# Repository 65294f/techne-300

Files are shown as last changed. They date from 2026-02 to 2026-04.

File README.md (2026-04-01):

<h1 align="center">Techne-300</h1>

<p align="center">
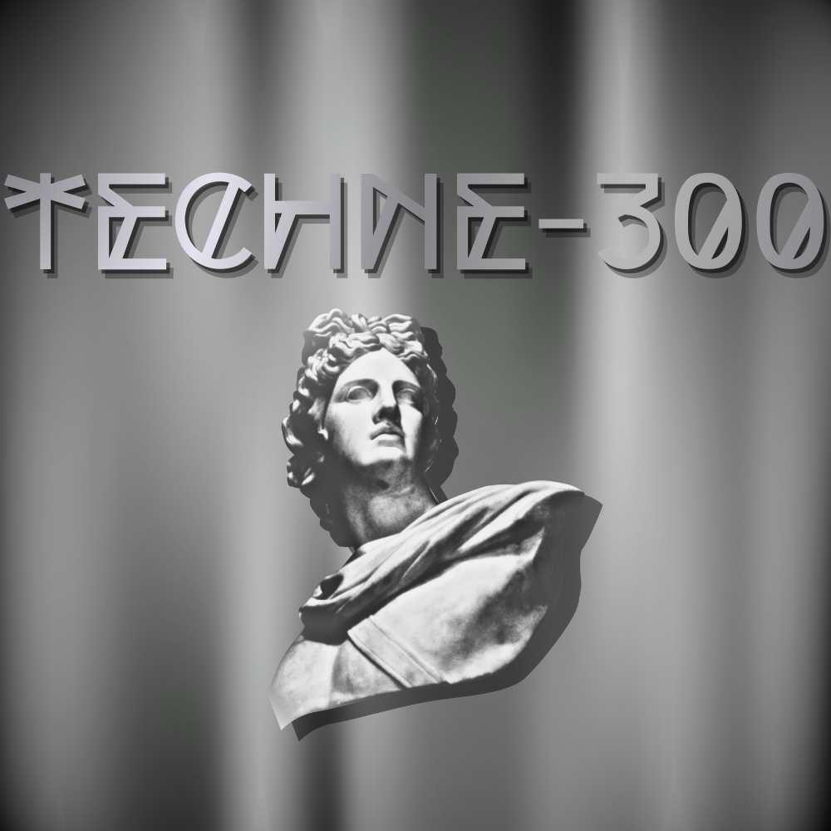
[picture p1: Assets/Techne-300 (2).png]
  
</p>

Inspired by builds like Chris Borges' printed CNC. Using thin-walled prints with threaded rods and concrete to add weight and structure on a budget. 
The Techne-300 is a simple CNC mill primarily made of 3D printed and readily available parts. It is designed for consistent milling for prototyping. 

<h4 align="center">
  BOM at the bottom of the README and 
<a href="https://docs.github.com)](https://github.com/65294f/techne-300/blob/main/Techne-300-part-list.csv">Part-list for amounts, STLs, filament, and print time for 3D printed parts.</a>
</h4>
<h3 align="center"> in the .csv BOM parts marked (purchased) are not added to the total cost and do not need funding.</h3>

I wanted to make this to help my FTC team quickly prototype parts that would normally take weeks to make or get. We have tons of innovative design ideas that are impossible for us to bring into reality without a CNC machine. This build is supposed to be iterated and improved over time for whatever application is needed. I wanted to make an interesting machine, something that hadn’t been made before — that’s why I went for the movement and the structure that I designed.

<h1 align="center">Design</h1>
This design started on paper, just small ideas that compounded into the machine you see now.

<p align="center">
  wiring
</p>

<p align="center">
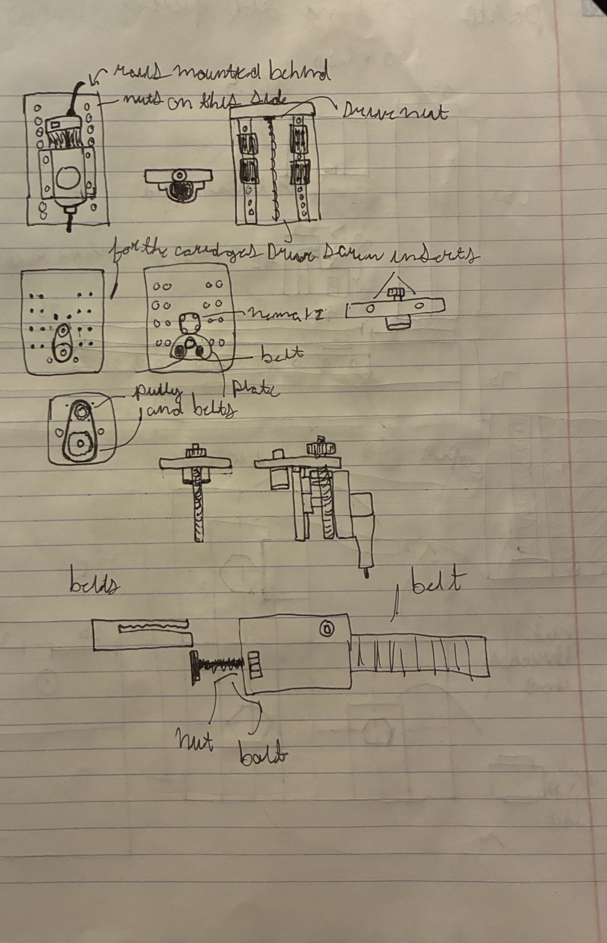
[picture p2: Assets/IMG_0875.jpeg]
  
</p>

<h1 align="center">Structure</h1>

The structure was inspired by Chris Borges' 3D printed CNC machine. It uses concrete-filled thin-walled 3D parts to add weight and structure while keeping prices low. To add more structure for the parts, 5/16 in threaded rod is run through the thin-walled parts and secured with nuts. 

<p align="center">
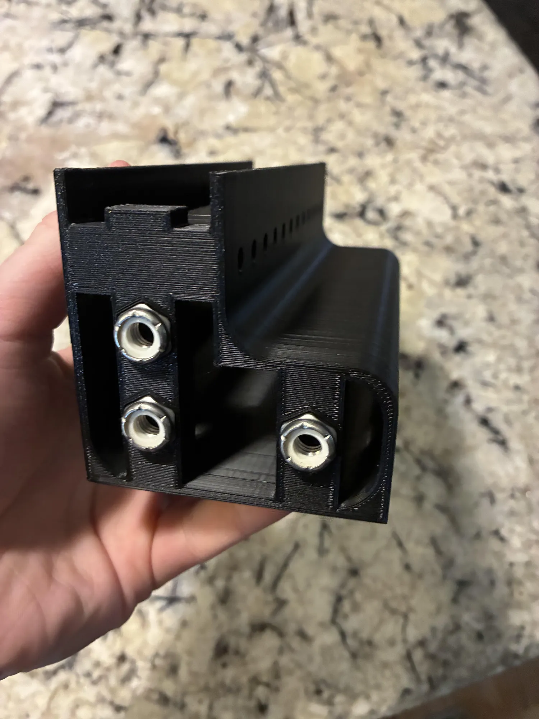
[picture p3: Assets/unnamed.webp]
  
</p>

The parts' thin walls are connected to prevent spreading from the weight of the concrete. This came after a few iterations of printed prototypes. 
The main structure is made of a single 3D printed part repeated 14 times with repeated corner pieces to reduce complexity. 

<p align="center">
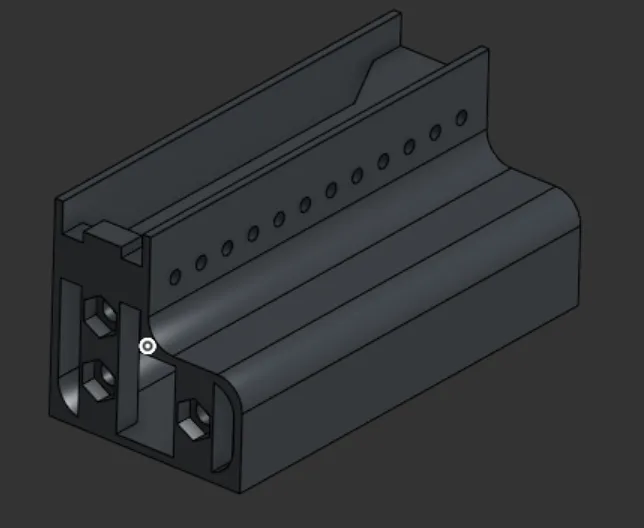
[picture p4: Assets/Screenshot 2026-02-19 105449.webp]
  
</p>

<p align="center">
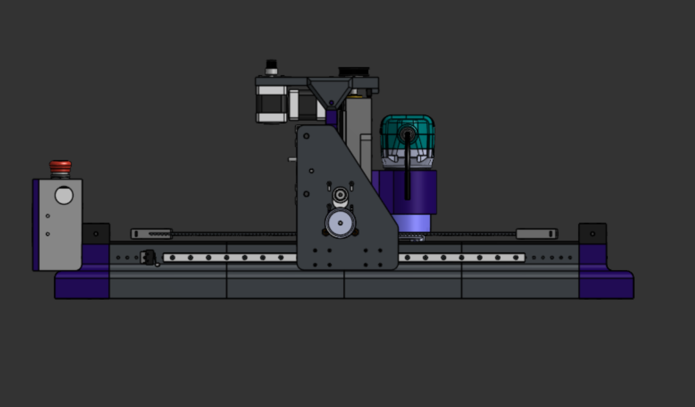
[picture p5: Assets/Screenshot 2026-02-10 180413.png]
  
</p>

<p align="center">
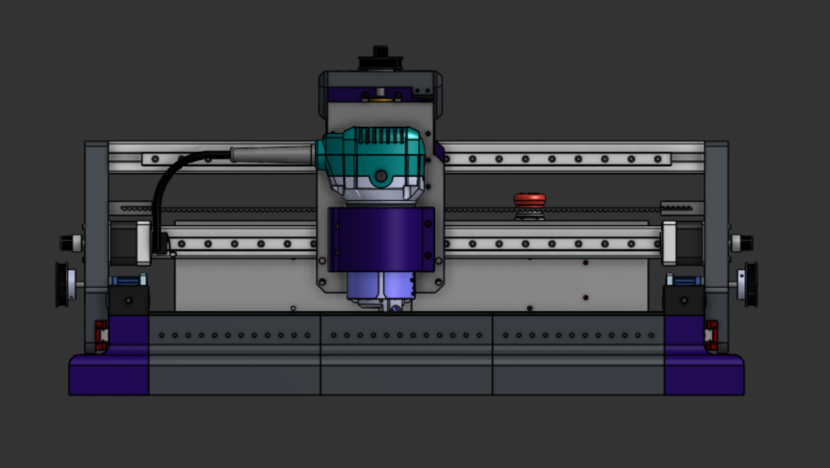
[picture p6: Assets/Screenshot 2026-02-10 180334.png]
  
</p>

<p align="center">
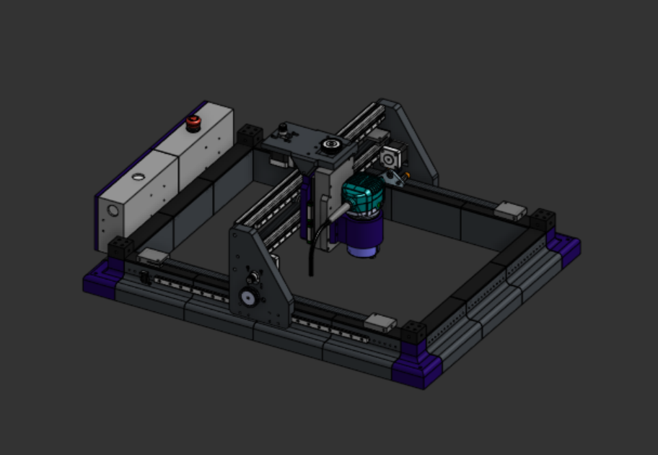
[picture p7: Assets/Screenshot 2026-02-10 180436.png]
  
</p>

<h1 align="center">Construction</h1>
The construction consists of two main parts: the base and the gantry. A full build guide will be able to be eventually found <a href="https://docs.google.com/document/d/1vw35Qro_V9RjRC6oUcMq-4XFSKVUzZ7_NZ20Waa5mPg/edit?usp=sharing"> HERE! 

<h1 align="center">Base</h3>

For the base, 3 nuts are placed in the holes and threaded rod is run through 2 groups of 3 and 2 groups of 4. The pieces are then assembled with the corners and glued/melted together. 

<p align="center">
  wiring
</p>

<p align="center">
  wiring
</p>

Concrete (concrete used cannot have any aggregate or the pour will be very difficult) is then poured into the empty space, and the back side of an electric sander is used to make sure that no air bubbles or unfilled spaces are left. The caps are pressed on and it is left to set. Heat-set inserts are pushed into the long side and then the linear rails are secured to the sides with M3 screws.

<h1 align="center">Gantry</h3>

The first step of gantry construction is screwing in the main 3D printed gantry pieces into the linear slides. The T-slot extrusion is then tapped and the linear rails are secured on with the T-nuts. You then screw the extrusion between the main gantry pieces. The Z-axis is then secured onto the linear rails.

<p align="center">
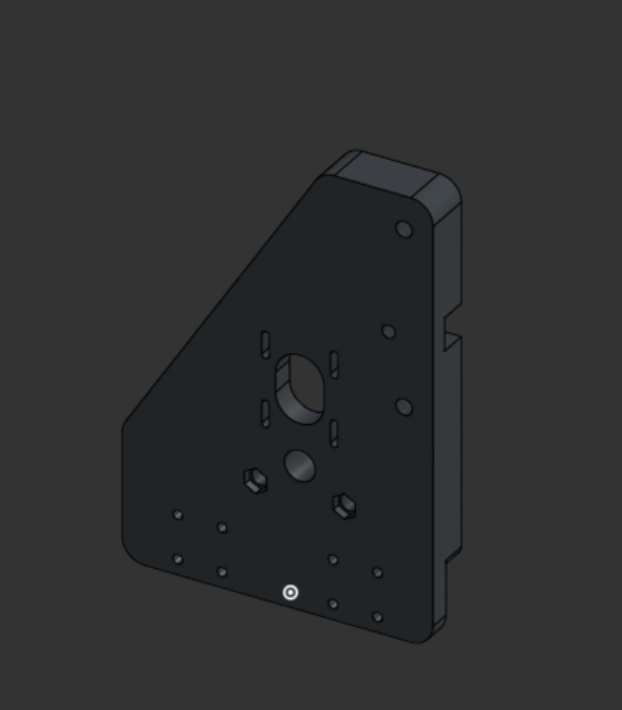
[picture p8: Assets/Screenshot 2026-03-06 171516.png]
  
</p>

<p align="center">
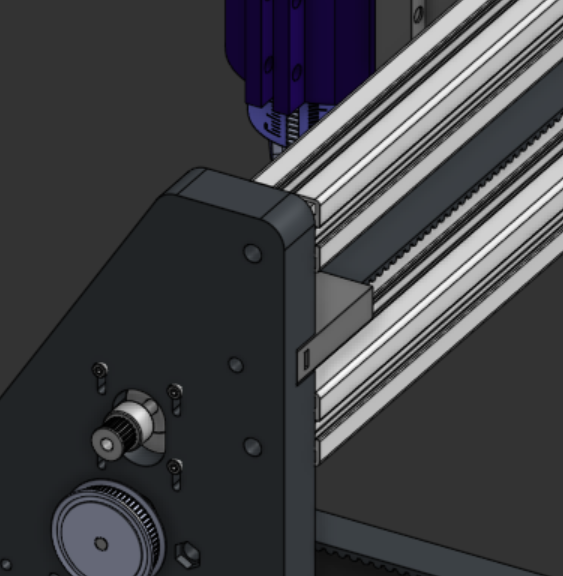
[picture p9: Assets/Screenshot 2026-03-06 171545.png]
  
</p>

For this project I used:
<h4>
<a href="https://github.com/winder/Universal-G-Code-Sender">Universal G-Code Sender</a>
</h4>
<h4>
<a href="https://www.onshape.com/en/">Onshape</a>
</h4>
For inspiration: <h4>
<a href="https://www.youtube.com/watch?v=L8t82OQXefM">Chris Borges</a>
and 
<a href="https://www.youtube.com/watch?v=ctyLjOHg7Ag">Ivan Miranda</a>
</h4>

<h1 align="center">Bill of Materials</h1>
<h3 align="center">Parts marked (purchased) are not added to the total cost and do not need funding.</h3>

| Part | Link | Amount | Price |
|---|---|---|---|
| (Purchased) Threaded Rod 5/16in. x 6 ft | [homedepot](https://www.homedepot.com/p/Everbilt-5-16-in-x-6-ft-Zinc-Plated-Steel-Coarse-Threaded-Rod-23021/332733633) | x4 | $23.92 |
| (Purchased) Hex Nut 5/16 in. | [homedepot](https://www.homedepot.com/p/Everbilt-5-16-in-18-Zinc-Plated-Hex-Nut-100-Pack-801740/204274104) | x1 | $2.18 |
| (Purchased) Concrete Mix 80 lb. | [homedepot](https://www.homedepot.com/p/Quikrete-80-lb-Concrete-Mix-110180/100318511) | x1 | $5.98 |
| MGN12 Linear Rail Guide 500mm | [aliexpress](https://www.aliexpress.us/item/3256806930596644.html) | x2 | $98.00 |
| Nema 17 Stepper | [amazon](https://www.amazon.com/NEMA17-Stepper-Torque-Bipolar-MOTOU/dp/B07RZHWYQ9) | x1 | $32.99 |
| Aluminum 5mm Bore 2GT Pulley | [aliexpress](https://www.aliexpress.us/item/2251832795479948.html) | x3 | $12.18 |
| 5mm x 330 mm steel rod | [aliexpress](https://www.aliexpress.us/item/3256805290944526.html) | x1 | $3.15 |
| 10 Teeth HTD 5M | [aliexpress](https://www.aliexpress.us/item/3256807463348700.html) | x3 | $16.11 |
| Ball Bearings | [aliexpress](https://www.aliexpress.us/item/3256805135171835.html) | x3 | $5.07 |
| Flanged Ball Bearings | [aliexpress](https://www.aliexpress.us/item/3256808460014090.html) | x1 | $5.61 |
| 150mm Lead Screw | [aliexpress](https://www.aliexpress.us/item/3256801899005803.html) | x1 | $4.99 |
| 60 Teeth Pulley | [aliexpress](https://www.aliexpress.us/item/3256808471298920.html) | x1 | $3.39 |
| Power Supply | [aliexpress](https://www.aliexpress.us/item/3256802657514911.html) | x1 | $5.01 |
| CNC Shield | [aliexpress](https://www.aliexpress.us/item/3256806291794239.html) | x1 | $8.27 |
| Emergency Stop | [aliexpress](https://www.aliexpress.us/item/3256810118000497.html) | x1 | $3.23 |
| Timing Belt | [aliexpress](https://www.aliexpress.us/item/3256810100027326.html) | x1 | $7.11 |
| 150mm Linear Rail | [amazon](https://www.amazon.com/uxcell-Sliding-Carriage-Bearing-Printers/dp/B0D54LDBHN) | x1 | $18.69 |
| 20x20 extrusion | [jlcmc](https://jlcmc.com/product/s/T01/TXCX/extruded-aluminum-t-slot-15-series(gb)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) | x1 | $1.89 |
| (Purchased) Makita router | [inventables](https://www.inventables.com/products/makita-router?variant=41037047398457) | x1 | N/A |
| Heated inserts | [amazon](https://www.amazon.com/Yaocom-Inserts-Threaded-Printing-Components/dp/B0DG59PW2R) | x1 | $9.99 |
| Micro Limit Switch | [amazon](https://us.amazon.com/HiLetgo-KW12-3-Roller-Switch-Normally/dp/B07X142VGC) | x1 | $5.99 |
| M3 T Nuts | [amazon](https://www.amazon.com/HELIFOUNER-Pieces-2020-Aluminum-Profile/dp/B0B1LTNX7F) | x1 | $4.99 |
| (Purchased) M3 Screws Assortment Kit | [amazon](https://www.amazon.com/Screws-Assortment-Plated-Socket-Washers/dp/B0D3X5CT2J) | x1 | $7.99 |
| (Purchased) 4kg PLA | [amazon](https://us.amazon.com/SUNLU-2-0-Filament-Stronger-Dimensional/dp/B0DGXFXP45) | x1 | $42.99 |

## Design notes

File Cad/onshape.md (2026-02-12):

<h1 align="center">onshape cad link</h1>

<h4 align="center">
<a href="https://cad.onshape.com/documents/1772326699bf1130a6529598/w/907cdc5ddbb09328c3f2774f/e/d35b3060a68eec815520a78b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">Onshape</a>
</h4>

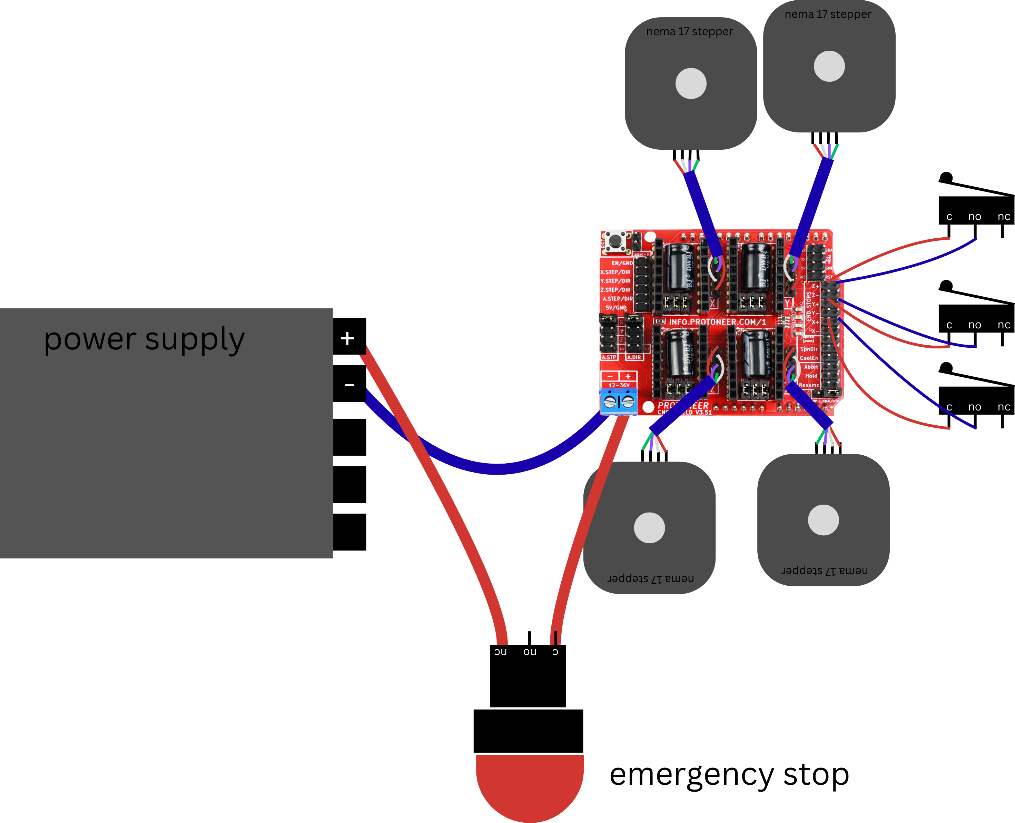
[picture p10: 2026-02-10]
c.png

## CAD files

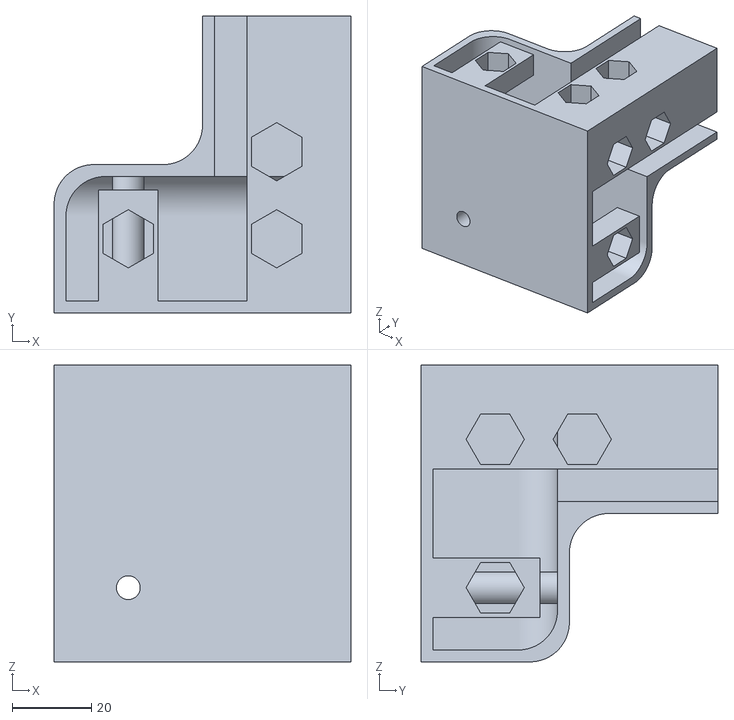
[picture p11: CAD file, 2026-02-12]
Parts/plastic print - Part 10.stl
75.0 x 75.1 x 75.0

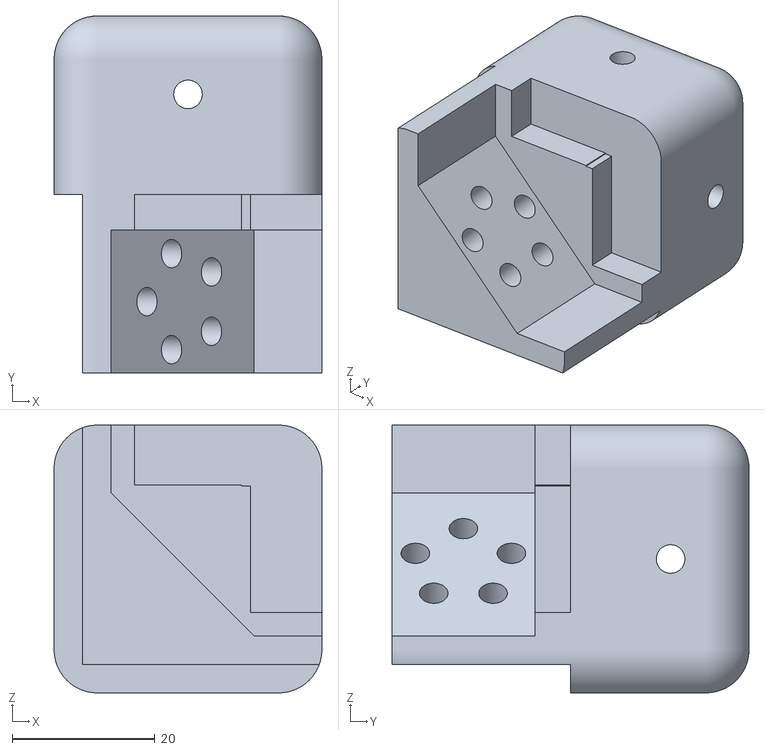
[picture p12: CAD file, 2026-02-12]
Parts/plastic print - Part 41.stl
37.5 x 50.0 x 37.5

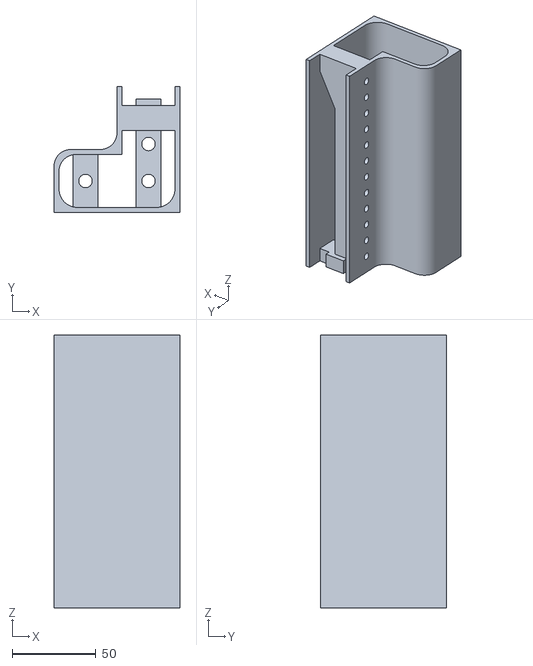
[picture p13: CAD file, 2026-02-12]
Parts/plastic print - Part 9.stl
75.0 x 75.0 x 162.5

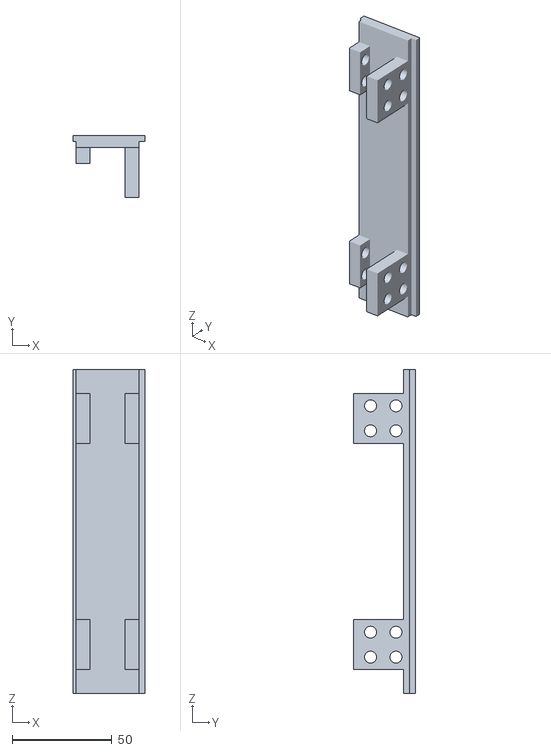
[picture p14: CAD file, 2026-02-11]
Parts/plastic print - Part 11.stl
36.0 x 31.0 x 162.5

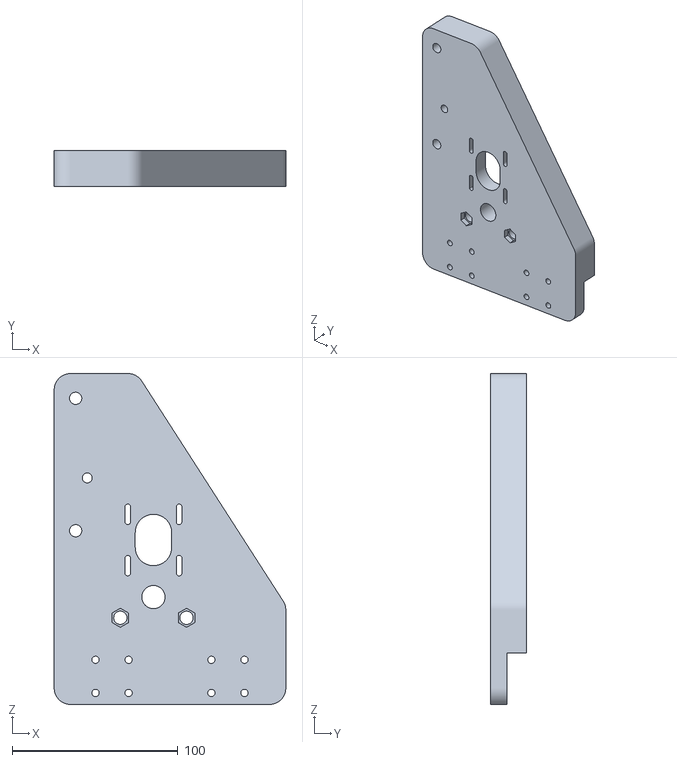
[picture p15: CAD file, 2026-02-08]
Parts/techne-300 - Part 26.stl
140.0 x 22.0 x 200.0

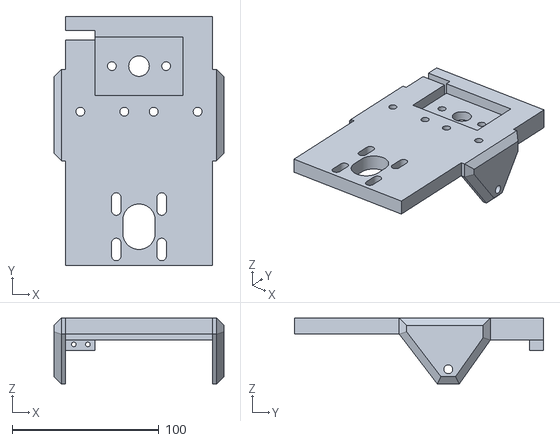
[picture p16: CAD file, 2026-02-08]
Parts/techne-300 - Part 24.stl
116.0 x 170.0 x 45.0

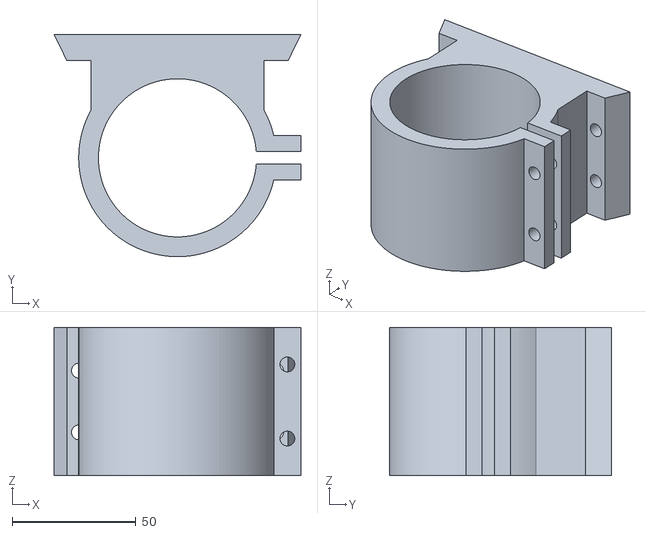
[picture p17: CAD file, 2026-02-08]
Parts/techne-300 - Part 17.stl
100.0 x 90.0 x 60.0

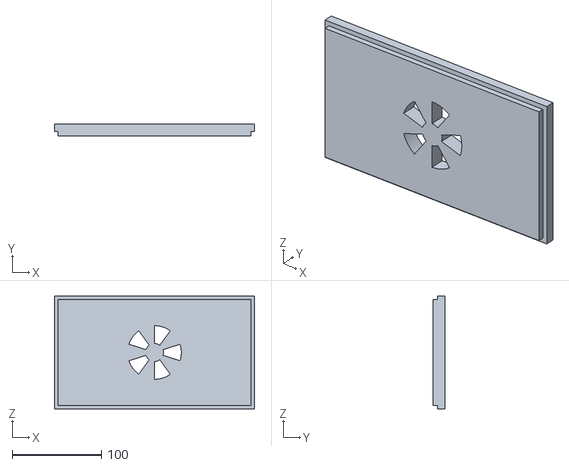
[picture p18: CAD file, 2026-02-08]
Parts/techne-300 - Part 40.stl
223.5 x 13.0 x 126.0

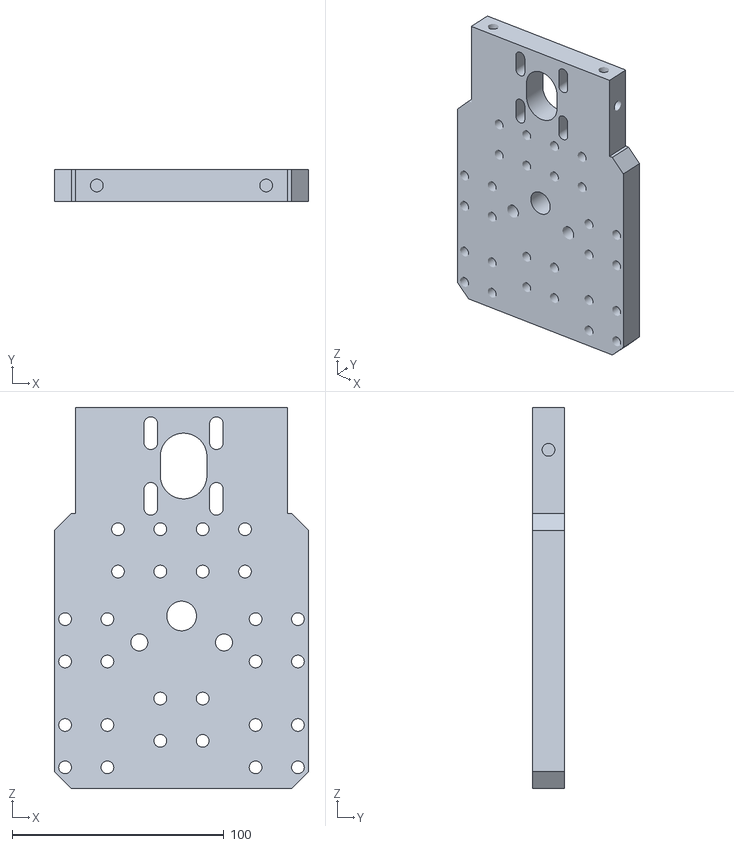
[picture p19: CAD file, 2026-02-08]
Parts/techne-300 - Part 15.stl
120.0 x 15.0 x 180.0

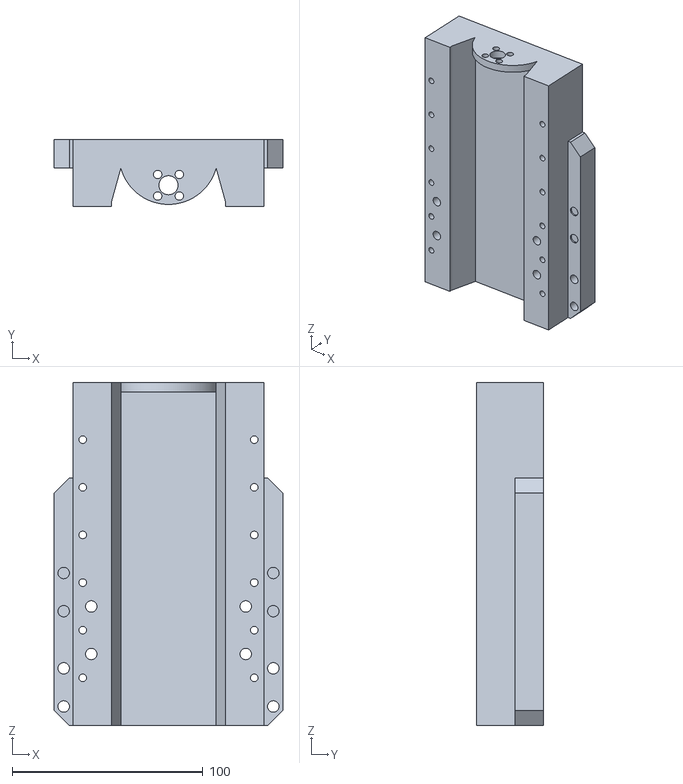
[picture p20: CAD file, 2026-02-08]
Parts/techne-300 - Part 16.stl
120.0 x 35.2 x 180.0

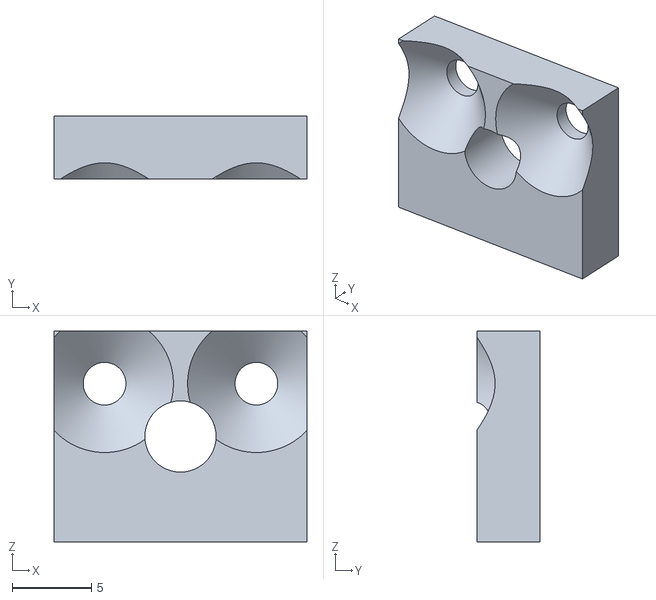
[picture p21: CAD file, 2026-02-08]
Parts/techne-300 - Part 35.stl
16.0 x 4.00 x 13.3

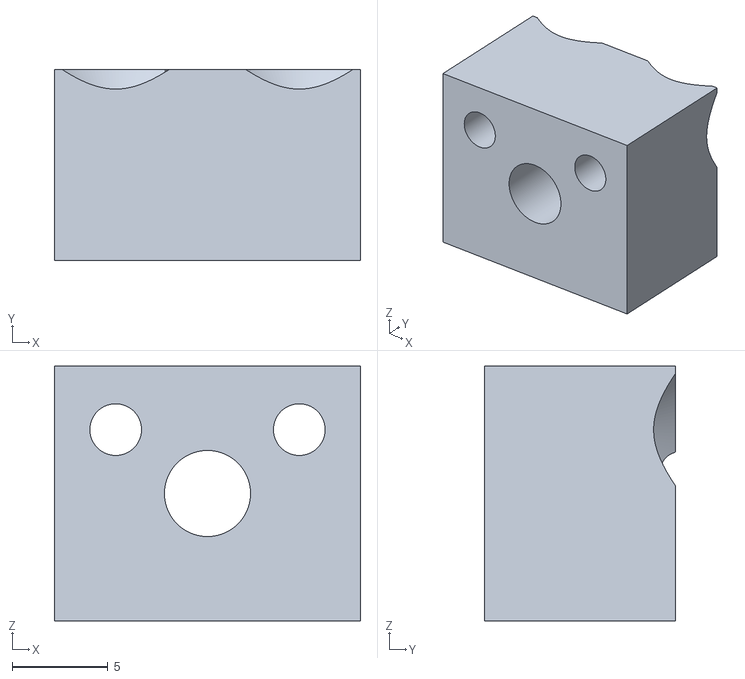
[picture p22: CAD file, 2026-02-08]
Parts/techne-300 - Part 39.stl
16.0 x 10.0 x 13.3

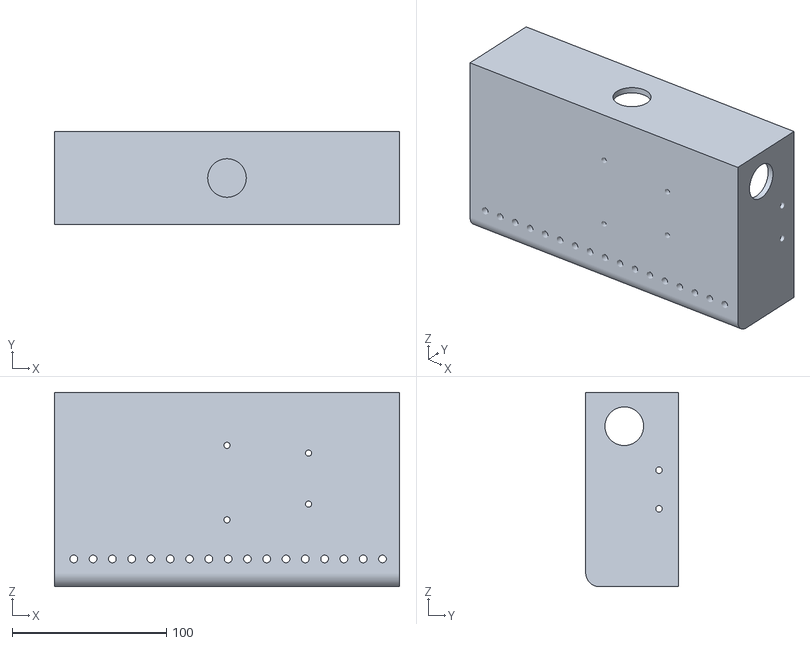
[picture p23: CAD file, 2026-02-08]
Parts/techne-300 - Part 34.stl
223.5 x 60.0 x 126.0

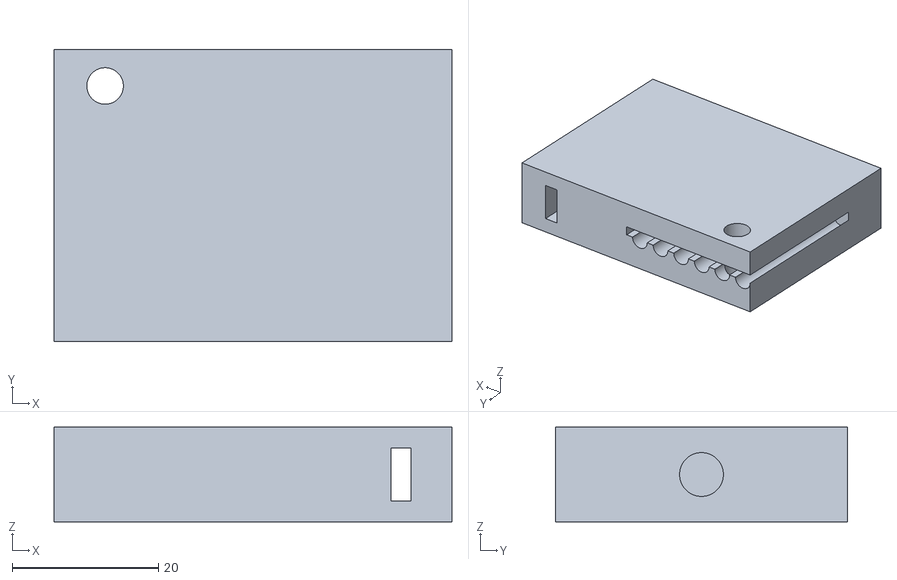
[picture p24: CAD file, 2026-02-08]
Parts/techne-300 - Part 23.stl
54.5 x 40.0 x 13.0

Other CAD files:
Parts/techne-300 - Part 13.stl
Parts/techne-300 - Part 14.stl

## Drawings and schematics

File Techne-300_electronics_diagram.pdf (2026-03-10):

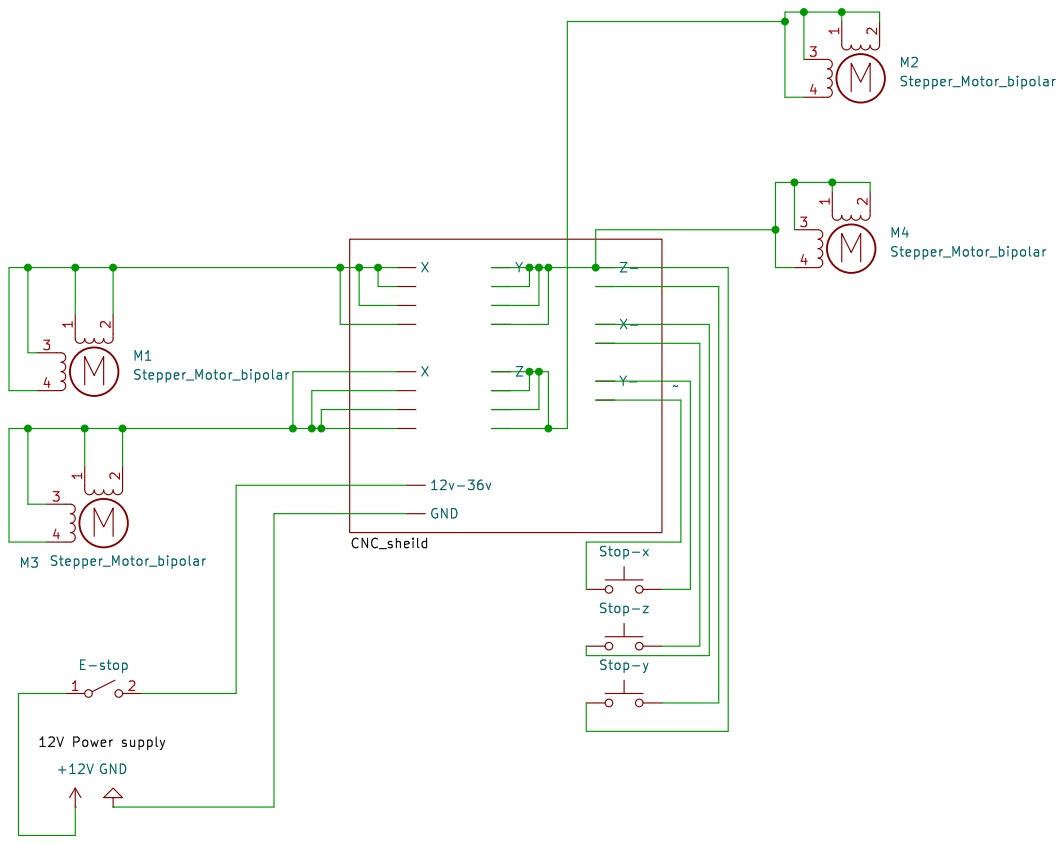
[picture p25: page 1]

Id: 1/1 Title: File: Techne-300.kicad_sch Sheet: /

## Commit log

2026-02-08 Rename Screenshot 2026-02-08 171658.png to wiring_diagram.png
2026-02-09 Update and rename Techne-300 - Sheet1 (1).csv to Techne-300_part_list.csv
    [Techne-300_part_list.csv]
2026-02-09 Update and rename Techne-300 - Sheet1 (2).csv to Techne-300-part-list.csv
    [Techne-300-part-list.csv]
2026-02-10 Update and rename Techne-300 - Sheet1 (3).csv to Techne-300 -part-list (3).csv
    [Techne-300 -part-list (3).csv]
2026-02-10 Update and rename Techne-300 -part-list (3).csv to Techne-300 -part-list.csv
    [Techne-300 -part-list.csv]
2026-02-11 Rename techne-300 (3).step to techne-300_Assembly.step
    [techne-300_Assembly.step]
2026-02-12 Update and rename Techne-300 - Sheet1 (4).csv to Techne-300-part-list.csv
    [Techne-300-part-list.csv]
2026-02-12 Rename techne-300 (4).step to techne-300.step
    [techne-300.step]
2026-02-12 Update and rename Techne-300 - Sheet1 (5).csv to Techne-300-part-list.csv
    [Techne-300-part-list.csv]
2026-02-25 Update and rename Techne-300 - Sheet1 (6).csv to Techne-300-part-list.csv
    [Techne-300-part-list.csv]
2026-03-11 Update and rename Techne-300 - Sheet1 (7).csv to Techne-300-BOM.csv
    [Techne-300-BOM.csv]
